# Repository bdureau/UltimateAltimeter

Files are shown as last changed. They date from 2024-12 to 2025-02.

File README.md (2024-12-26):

# UltimateAltimeter
This altimeter uses the TS-ESP32-S3 board without any additional components
You can find it on Aliexpress
https://vi.aliexpress.com/w/wholesale-TS%2525252dESP32%2525252dS3.html

That board has a BME280 sensor as well as a QMI8658 sensor.
You can measure the pressure (and derive the altitude from it). It also has a 3 axes accelerometer and well as gyroscope

The board is based on the Adafruit ESP32 S3 TFT Feather

https://cdn-learn.adafruit.com/downloads/pdf/adafruit-esp32-s3-tft-feather.pdf

https://github.com/adafruit/Adafruit-ESP32-S3-TFT-Feather-PCB/blob/main/Adafruit%20ESP32-S3%20TFT%20Feather%20Pinout.pdf

The board looks like this

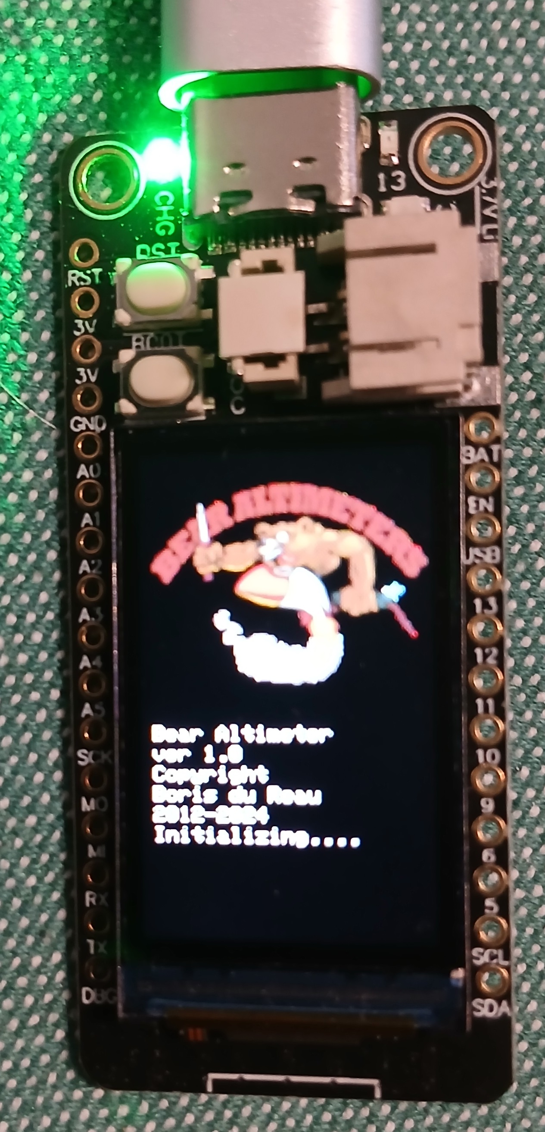
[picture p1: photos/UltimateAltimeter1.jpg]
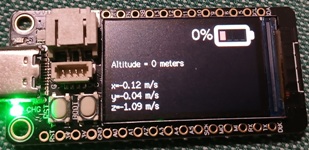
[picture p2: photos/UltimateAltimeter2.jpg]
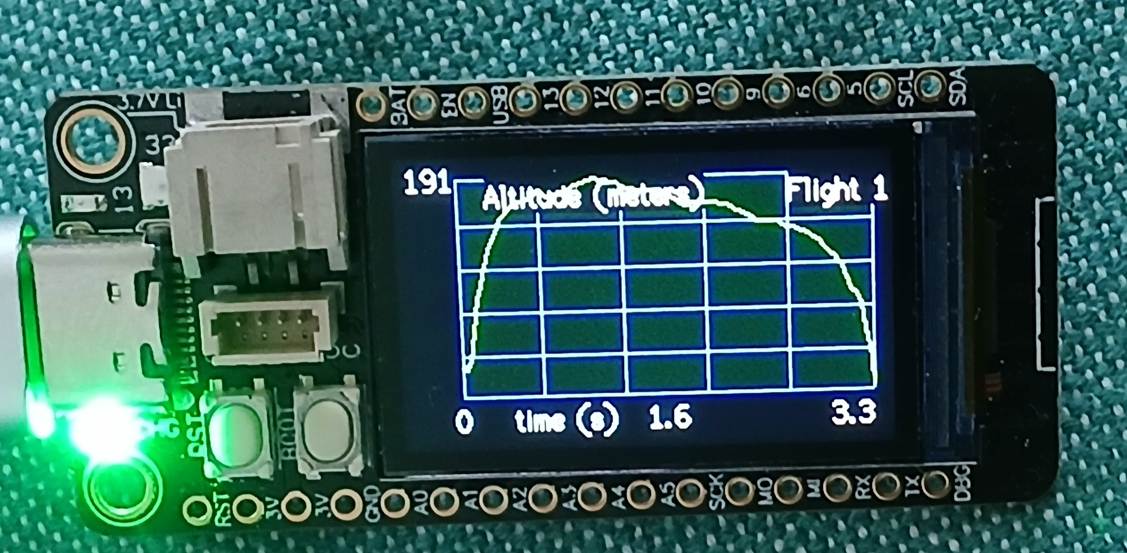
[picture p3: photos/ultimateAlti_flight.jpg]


# Building the code

You will need to download the Arduino ide from the [Arduino web site](https://www.arduino.cc/). 
Make sure that you install ESP32 support. 

2 versions are provided one that uses the preference library to store the flight.
https://github.com/bdureau/UltimateAltimeter/tree/main/UltimateAltimeter

and another one that uses the LittleFS library
https://github.com/bdureau/UltimateAltimeter/tree/main/UltimateAltimeterLittleFS

The project depend on the following libraries
  - TFT
  - Button2
  - TFT_eWidget
  - Preferences or LittleFS
  - BME280
  - SensorLib (used for the QMI8658 sensor)
    
You will need my fork of the TFT_eSPI
https://github.com/bdureau/TFT_eSPI

Compile with the following options:

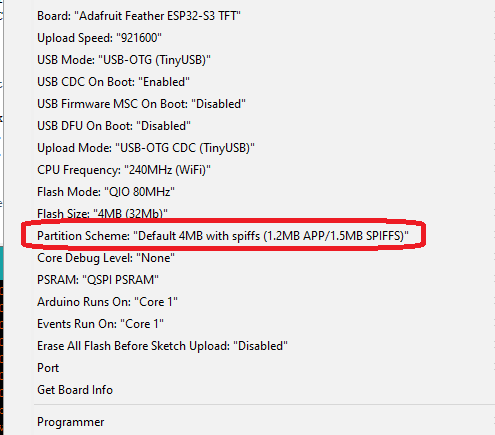
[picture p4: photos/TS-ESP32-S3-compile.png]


Prior to compiling go to the TFT_eSPI and open up the file User_Setup_Select.h

Comment out the following line
```
//#include <User_Setup.h> 
```
and uncomment the following line
```
#include <User_Setups/Setup400_Adafruit_Feather.h>
```

You will need to have the ESP32 board support version 2.0.14, anything higher than that may not work !!!

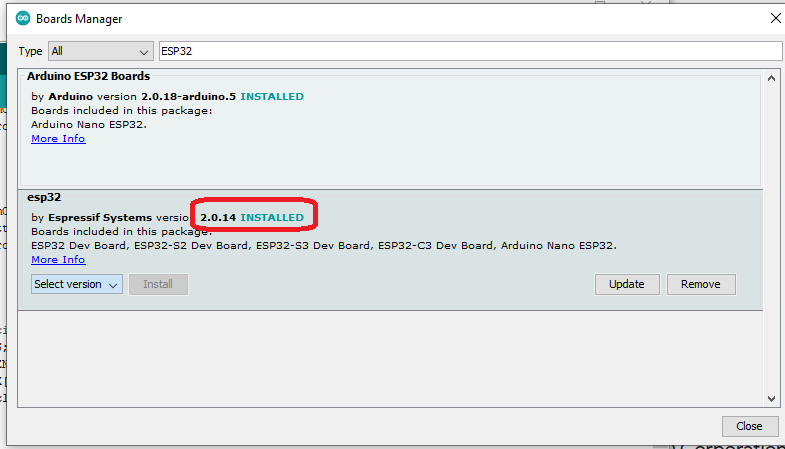
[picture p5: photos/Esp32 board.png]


# Contributing

If you want to contribute to the project just fork my project or send me some code. 

Report any issue or bug that you have

Suggestions and enhancement are welcome

The code is free for you to download and you do not need to buy anything from me. However it cost money to try out new boards, you need to buy them and fly them so if you want to financially help me you can donate via paypal

| Paypal | 
| ------ |
|  | 

# Disclaimer

I am not responsible for any damage that could happen. The code is provided as it is

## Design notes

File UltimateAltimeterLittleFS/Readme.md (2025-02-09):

This version uses the LittleFS library to store data. It might be slower but it can store a lot more data.
The following is recorded:
altitude, pressure, temperature, humidity and acceration on the 3 axis

Specific instruction to compile it
Make sure SPIFFS otherwise it will not store the data

As of version 0.5 I am switching to the BMP280 library from dvarrel (ver 1.0.3)
https://github.com/dvarrel/BMP280

use the following compilation directive #define USE_SLEEP_MODE to enable or disable the sleep mode

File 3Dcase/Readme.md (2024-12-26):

This is a case for the altimeter that can be 3D printed

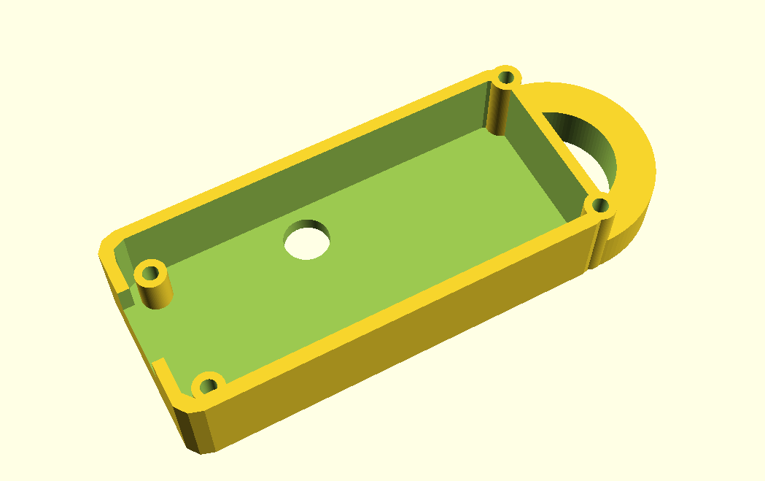
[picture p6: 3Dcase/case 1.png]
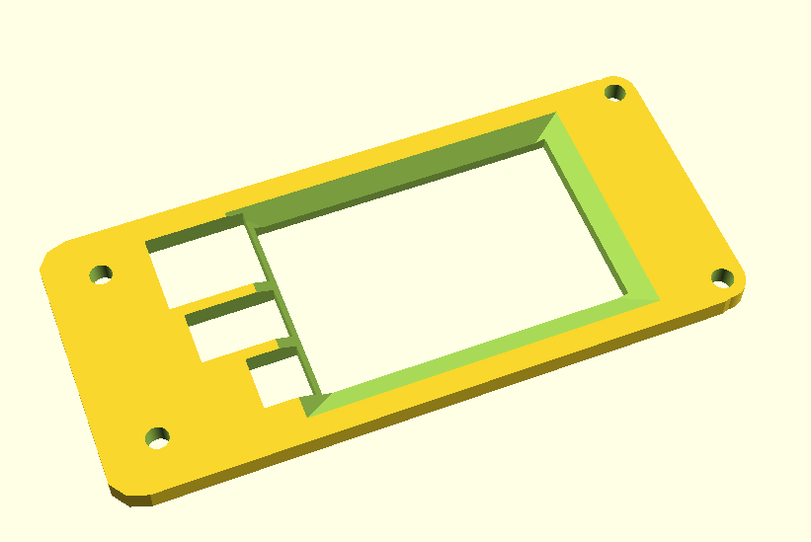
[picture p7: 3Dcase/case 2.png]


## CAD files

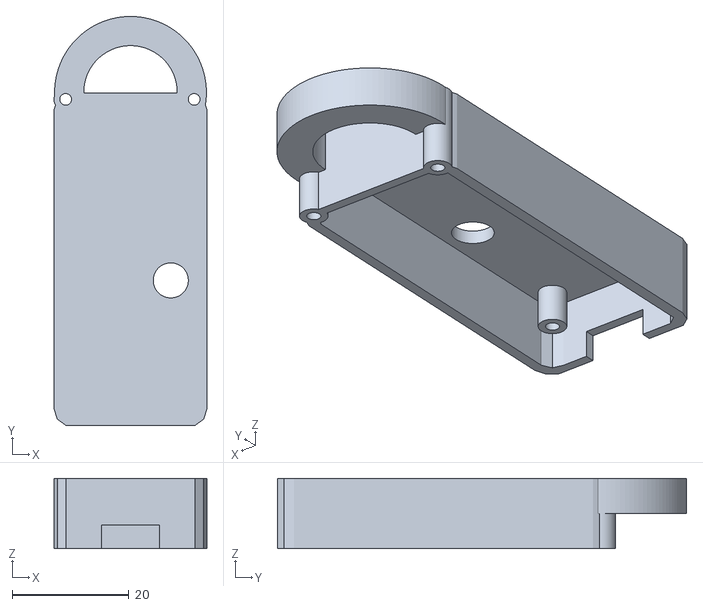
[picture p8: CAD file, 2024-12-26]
3Dcase/case_ts-esp32-s3altiV2.stl
26.2 x 70.1 x 12.0

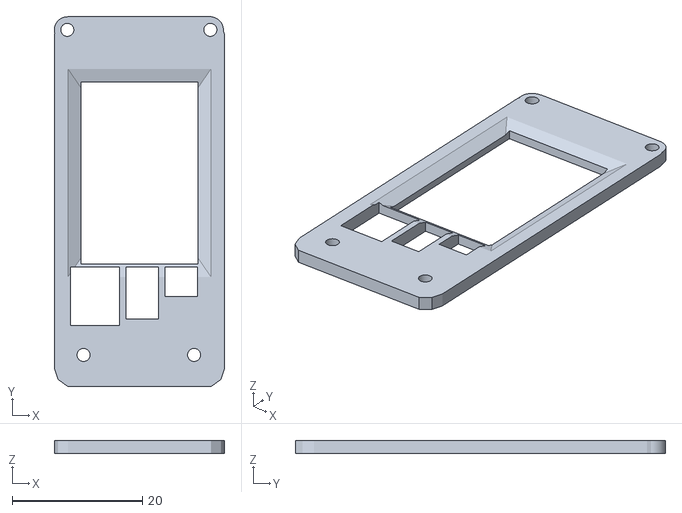
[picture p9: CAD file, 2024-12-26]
3Dcase/cover_case_ts-esp32-s3altiV2.stl
26.2 x 56.9 x 2.00

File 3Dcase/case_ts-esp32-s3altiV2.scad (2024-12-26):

/****************************************************************
* title: Alti case TS-ESP32-S3
* author: Boris du Reau
* version: 1.0
* date: 26/12/2024
* 
* Description: 
* Howto use it:
* Modify the variables values so that it fits to your rocket tube 
* then just click on "compile and render" 
* Note that all units ar metrics
*****************************************************************/

/* adjust variables here */ 

/* Do not modify anything after that unless you know what you are doing*/

module roundedcube(xdim, ydim, zdim,rdim) {
    hull(){
        translate([rdim, rdim,0]) cylinder(r=rdim, h=zdim);
        translate([xdim-rdim, rdim,0]) cylinder(r=rdim, h=zdim);
        translate([rdim, ydim -rdim,0]) cylinder(r=rdim, h=zdim);
        translate([xdim-rdim, ydim-rdim,0]) cylinder(r=rdim, h=zdim);
    }
}


module box() {
difference() {
    union() {
        difference() {
            union() {
                translate([0,0,-2])roundedcube(23 +(2*1.6), 54+ (2*1.6), 12,3); 
                difference() {
                    #translate ([(23 +(2*1.6))/2,54+ (2*1.6),4]) #cylinder(r=26/2, h=6, $fn=100);
                    #translate ([(23 +(2*1.6))/2,54+ (2*1.6),4]) #cylinder(r=16/2, h=6, $fn=100);
                }
            } 
            #translate ([1.6,1.6,-2]) roundedcube(23, 54, 10,2);  
        }     
        
        //case holes
        //#translate([0+2,2,4])cylinder(r=2, h=12, center = true, $fn =100);
        //#translate([0+28,2,4])cylinder(r=2, h=12, center = true, $fn =100);
        #translate([0+2,58-2,4])cylinder(r=2, h=12, center = true, $fn =100);
        #translate([0+24,58-2,4])cylinder(r=2, h=12, center = true, $fn =100); 
        
        //board holes
        #translate([0+2+2.5,2+3,6])cylinder(r=2, h=7, center = true, $fn =100);
        #translate([0+2+1.5+18,2+3,6])cylinder(r=2, h=7, center = true, $fn =100);
    }
    //case holes
    //#translate([0+2,2,0])cylinder(r=2/2, h=30, center = true, $fn =100);
    //#translate([0+28,2,0])cylinder(r=2/2, h=30, center = true, $fn =100);
    #translate([0+2,58-2,0])cylinder(r=2/2, h=30, center = true, $fn =100);
    #translate([0+24,58-2,0])cylinder(r=2/2, h=30, center = true, $fn =100);
    //board holes
    #translate([0+2+2.5, 2+3,5])cylinder(r=2/2, h=7, center = true, $fn =100);
    #translate([0+2+1.5+18, 2+3,5])cylinder(r=2/2, h=7, center = true, $fn =100);
    
    //usb port
    #translate([(23 +(2*1.6))/2,1,0])cube([10,2,4], center = true);
    //sensor hole
    #translate([20,25,4])cylinder(r=3, h=12, center = true, $fn =100);
}
    
}

module cover() {
difference() {
    union() {
        difference() {
            translate([0,0,0])roundedcube(23 +(2*1.6), 54+ (2*1.6), 2,3);     
        }
        //case holes
        //#translate([0+2,2,1])cylinder(r=2, h=2, center = true, $fn =100);
        //#translate([0+28,2,1])cylinder(r=2, h=2, center = true, $fn =100);
        #translate([0+2,55,1])cylinder(r=2, h=2, center = true, $fn =100);
        #translate([0+24,55,1])cylinder(r=2, h=2, center = true, $fn =100);
    }
    
    //case holes
    #translate([0+2,55,0])cylinder(r=2/2, h=30, center = true, $fn =100);
    #translate([0+24,55,0])cylinder(r=2/2, h=30, center = true, $fn =100);
    //board holes
    #translate([0+2+2.5,2+3,0])cylinder(r=2/2, h=30, center = true, $fn =100);
    #translate([0+2+1.5+18,2+3,0])cylinder(r=2/2, h=30, center = true, $fn =100);
    
    //window
    #translate([(23 +(2*1.6))/2,17.5+(31/2),2]) cube([18, 28, 4], center = true);
    #translate([(23 +(2*1.6))/2,17.5+(31/2),0])resize([22,32])rotate([0,0,45])cylinder(h=2, r1= 20, r2 = 32, $fn=4);
    
    #translate([2.5,9.5,0]) cube([7.5,9,4]);
    #translate([11,10.5,0]) cube([5,8,4]);
    #translate([17,14,0]) cube([5,4.5,4]);
} 
    
}

//box();
cover();

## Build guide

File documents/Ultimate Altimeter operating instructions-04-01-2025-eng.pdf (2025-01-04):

Ultimate Altimeter operating instructions

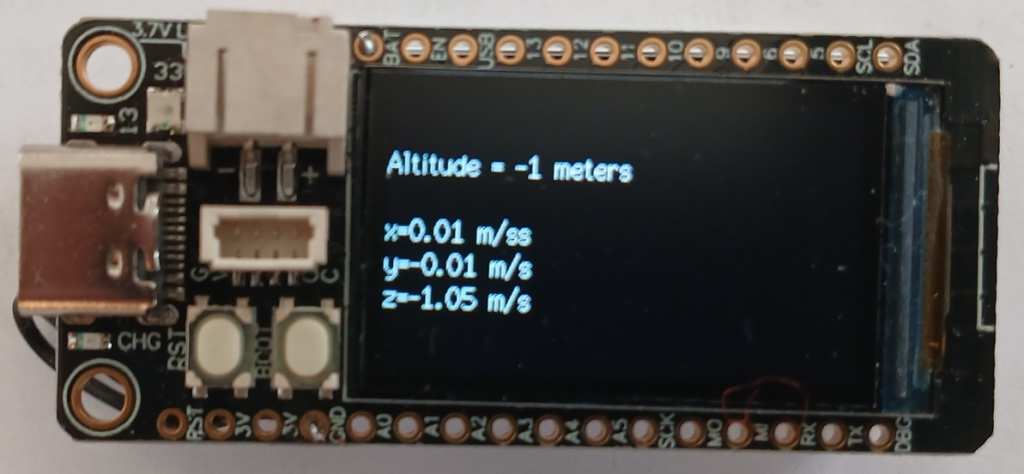
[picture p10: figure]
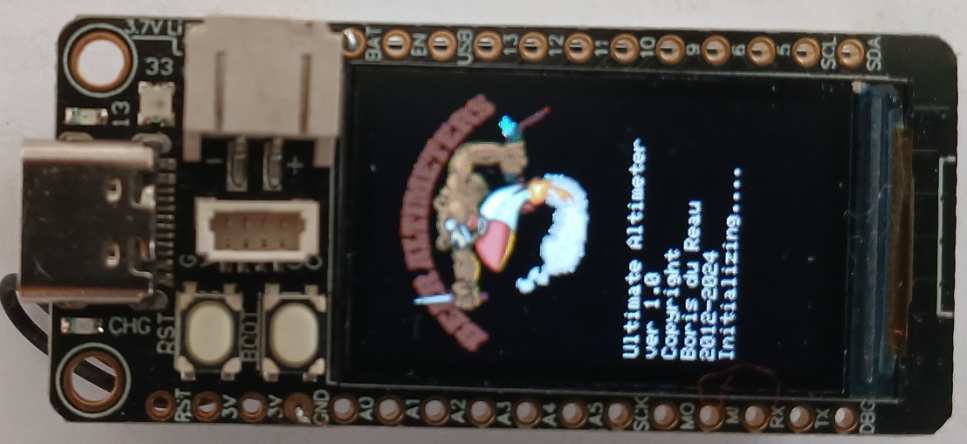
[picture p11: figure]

04/01/2025 | Copyright © Boris du Reau 2012-2025 | page 1

## Ultimate altimeter Operating instructions

Version | date | Author | Comments
1.0 | 04/01/2025 | Boris du Reau | Initial version

Rocket Type
Micro-max | Model Rocket | Mid power | High power | Water rocket
No | yes | yes | yes | yes

Category
Construction technic | Ground Support | Electronic | Other
| | X X

04/01/2025 | Copyright © Boris du Reau 2012-2025 | page 2

04/01/2025 | Copyright © Boris du Reau 2012-2025 | page 3

Goal

The goal of this document is to explain how to use the Ultimate altimeter that you just bought. The document assumes that you have already installed altimeters in a rocket payload bay.

Before your start
Remember that you can modify the program and behaviour of your altimeter.
The country where you live might not even allow the use of such device. You have to assume total legal responsibility for any damages or claims including personal injury that results from the use of this device. I shall not be responsible for the above. If you disagree with that, please do not build it or use it.

Related documentation
This document assumes that you have red the Bear Altimeters console documentation. This document will show you how to use the altimeter stand alone or with the console to view flights on a larger screen. I will also cover things such as flashing the altimeter from the Android Console.

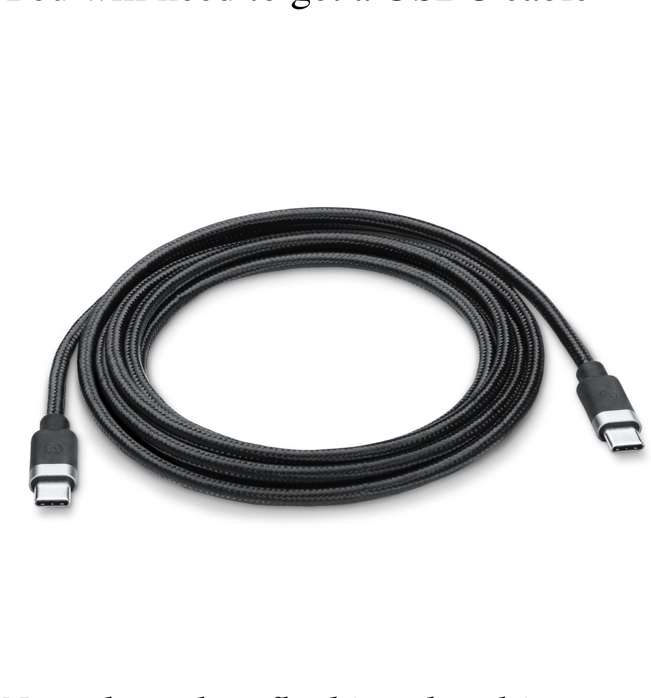
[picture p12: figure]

04/01/2025 | Copyright © Boris du Reau 2012-2025 | page 4

About the altimeter
The altimeter is made using a TS-ESP32-S3 board which contains an ESP32S3 micro controller from Espressif no additional custom board is required because the board already has a BME280 barometer and a QMI8658 sensor (accelerometer + gyroscope. The flights can be stored on the board no need of an additional EEPROM.
The firmware is written in C/C++ using the Arduino environment you can download the latest firmware from github
https://github.com/bdureau/UltimateAltimeter

If you are a developer you can build the firmware yourself using the Arduino environment and upload it to your board. Detailed instructions to build the code are available on the Github repository.

Flashing the altimeter firmware
The altimeter firmware can be flashed using the “BearConsole” application available on the Android playstore.
https://play.google.com/store/apps/details?id=com.altimeter.bdureau.bearconsole

Currently no application is available for Apple and I am not planning on doing any. Should any one want to write one the Android source code is available on my Github https://github.com/bdureau/BearConsole2

You will need to get a USBC cable

Note that when flashing the altimeter no need to configure the application to use USB, it will automatically do it because a USB cable is the only way to flash the altimeter, you cannot do it with a Bluetooth module.

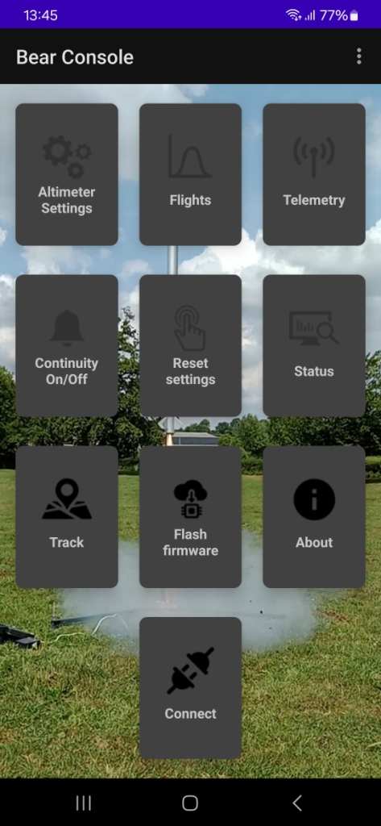
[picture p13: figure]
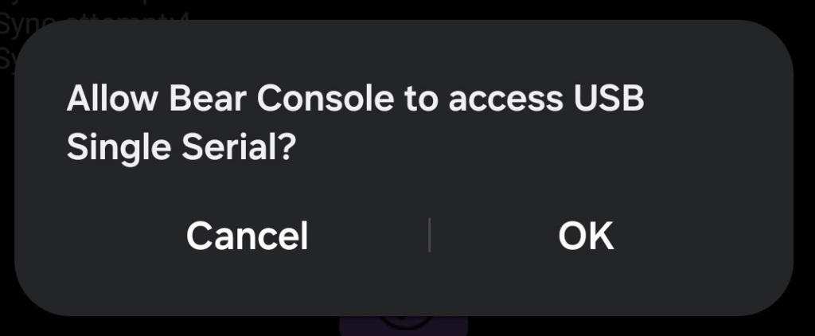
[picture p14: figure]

04/01/2025 | Copyright © Boris du Reau 2012-2025 | page 5

The following needs to be done to flash your board with a new firmware
- First install the application on an android device. Get it from the Android playstore https://play.google.com/store/apps/details?id=com.altimeter.bdureau.bearconsole
- Get a USB cable and connect your phone to the altimeter
- Open up the BearConsole application
- Tap on the flash firmware button
- Grant the permission

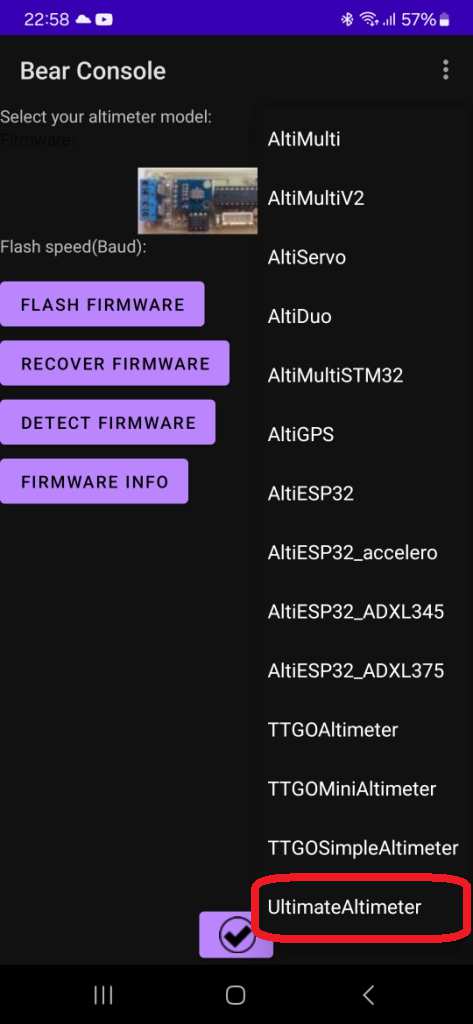
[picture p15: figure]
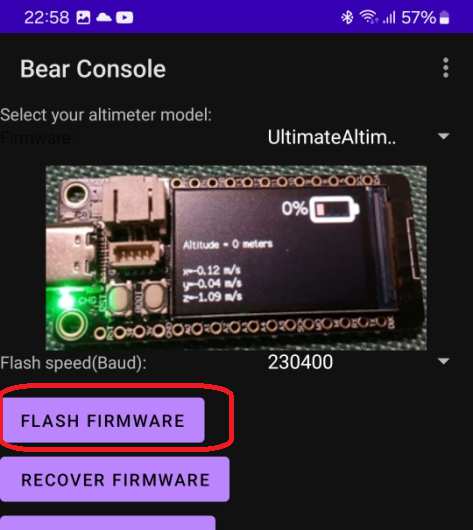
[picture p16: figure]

04/01/2025 | Copyright © Boris du Reau 2012-2025 | page 6
- Select your altimeter firmware. Make sure that you choose the appropriate firmware, if you don’t you will have unexpected behaviour.
- Tap on the flash firmware button

A popup will display with the firmware progress

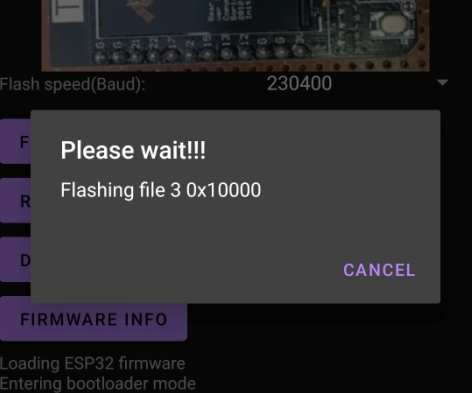
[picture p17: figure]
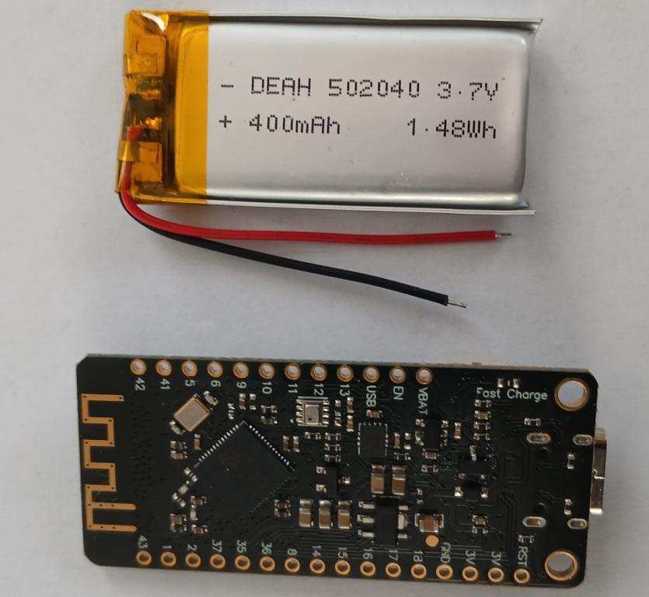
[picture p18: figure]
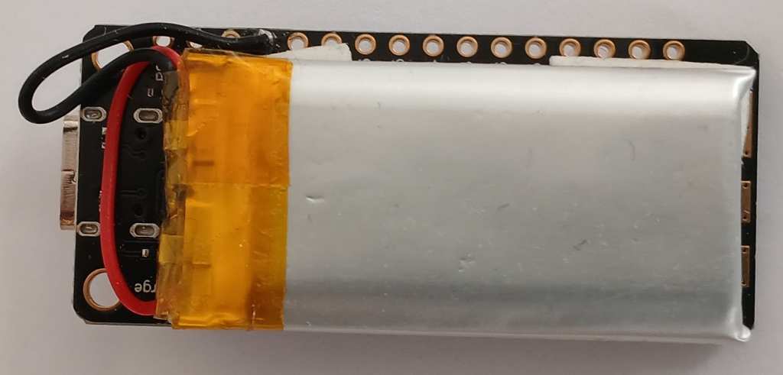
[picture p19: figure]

04/01/2025 | Copyright © Boris du Reau 2012-2025 | page 7

Flashing should take less than a minute when complete reset your altimeter.

Note that you need to make sure that the cable is connected during the entire upload of the firmware.

Choosing the power supply
The kit has been designed to use a 1S (3.7 Volts) battery. Using a poor quality battery may result in altimeter malfunction. You will need to get a JST plug compatible with your board or you can solder your 1S battery directly on the board (red wire on Vbat and black wire on GND). Be careful the TS-ESP32-S3 board JST plug is wired reverse; if you use a standard battery with a JST plug you will burn your board.

Charging the altimeter
The altimeter can be charged using a USBC cable and any USB port from a computer or from a USB charger. You will see the charge progress with the battery symbol.

Preparing the altimeter
When using the altimeter for the first time the altimeter must be initialized. First you need to blank the eeprom.
Power the altimeter by pressing button 2.
Then press button 2 for more than 10 seconds.
This will erase all flights.

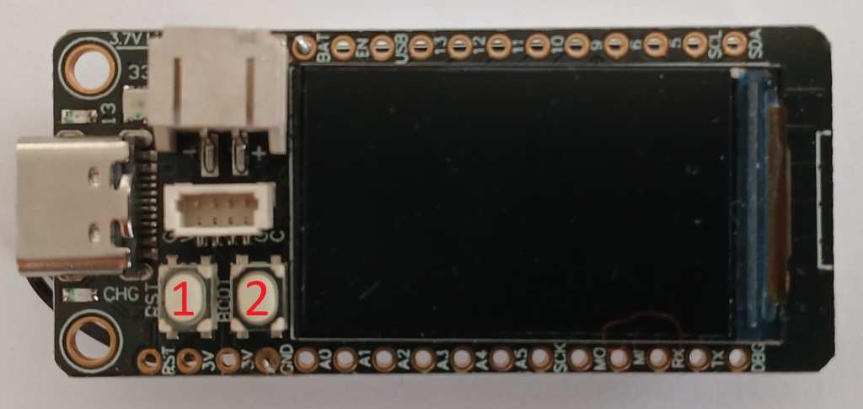
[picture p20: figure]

04/01/2025 | Copyright © Boris du Reau 2012-2025 | page 8

You are now left with an altimeter with no flights at all ready to be used.
Note that if you do not initialise your altimeter you may not be able to start recording flights.

Note that button 1 is the reset button; everything is done using only button 2.

Powering off the altimeter
You do not turn off your altimeter using a switch. By pressing button2 for more than 5 seconds you can put the altimeter in hibernate mode. Because it is in hibernate mode you need to make sure that you recharge your altimeter at least once a month otherwise your battery will get discharged under 3 volts and could be permanently damaged.
If you do not want to charge your altimeter, unplug your battery.

Installing the altimeter in the Rocket
The altimeter is very easy to install, just attach it to the nose cone. You will need to make sure that you have one or more vent holes to allow pressure exchanges.

Make sure that the electronic is protected from ejection smokes which are very corrosives and could damage the altimeter board very quickly.
However remember that you have a pressure sensor which needs to measure pressure changes to work out altitude changes… hence you need to drill a hole in your payload bay.

Using the altimeter
Now that you have everything installed in your rocket you can turn it on. The altimeter wait until lift off is detected. Lift off being by default reference altitude + 20 meters (this can be changed). Make sure that the altimeter is fully charged so that it can record the entire flight.

Reading your altimeter data without an Android device
You can read your data directly on the altimeter screen. The altimeter has been designed so that it can be used without an Android device; this will have limited functionalities but will allow you to quickly see your flight data when on the field.

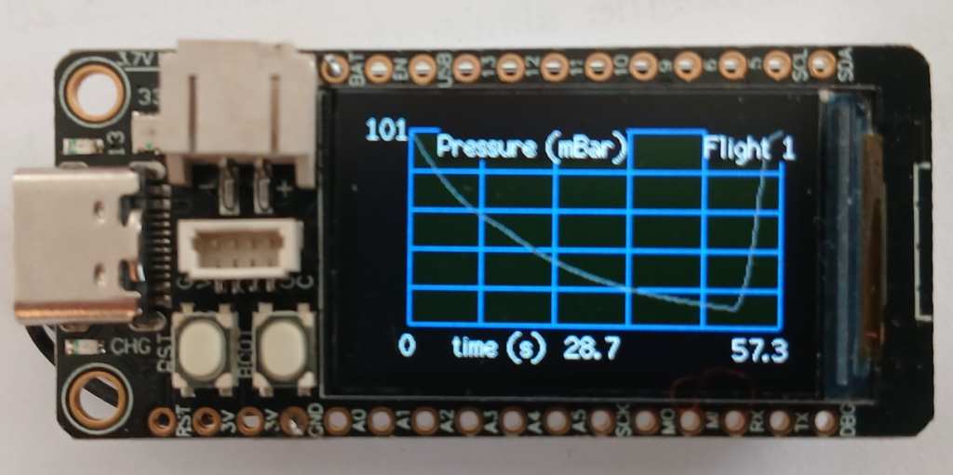
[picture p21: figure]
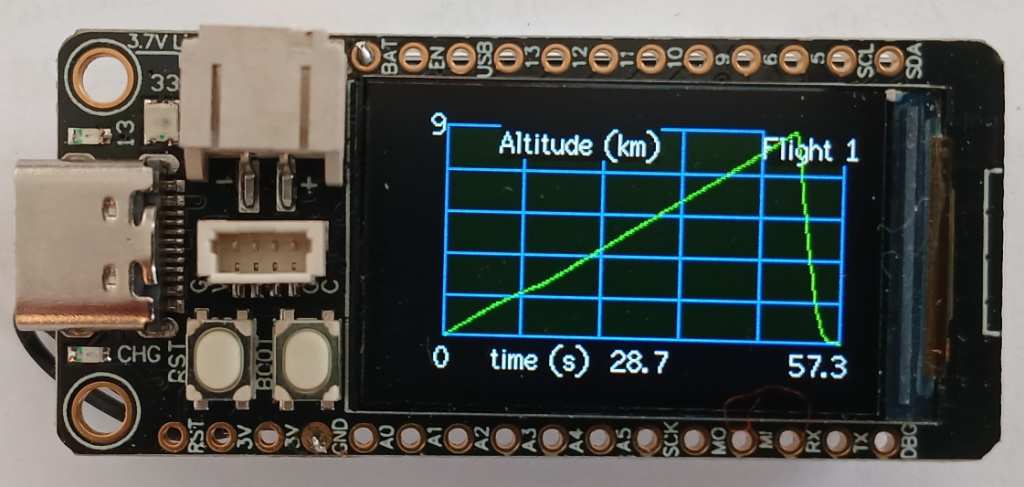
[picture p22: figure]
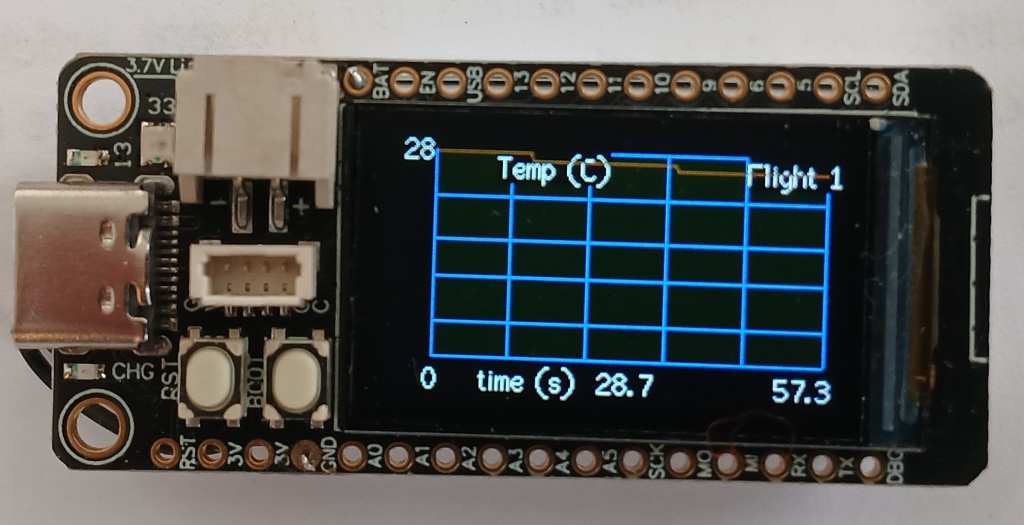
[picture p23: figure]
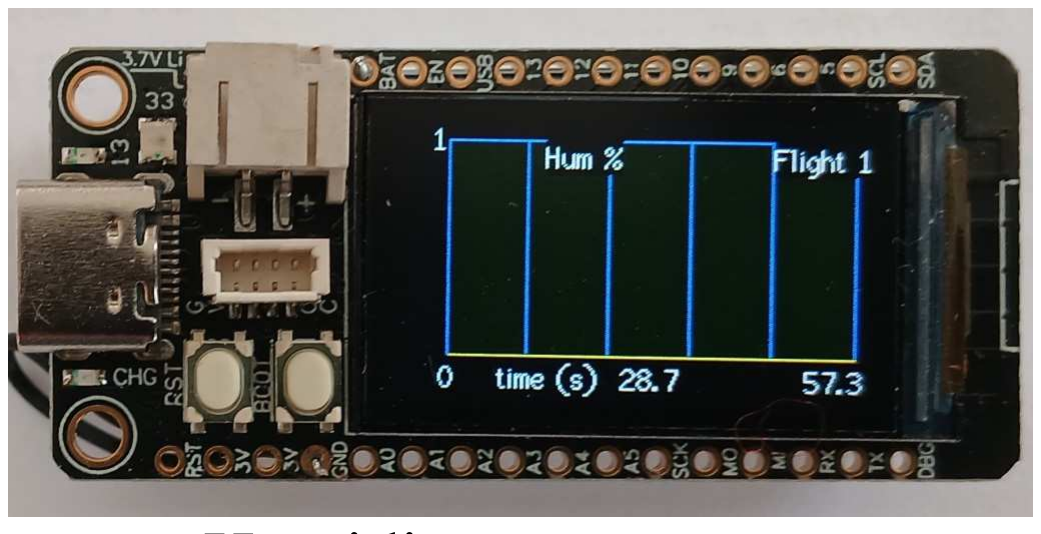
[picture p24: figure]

04/01/2025 | Copyright © Boris du Reau 2012-2025 | page 9

Retrieving your flight data
Press button 2 for more than 2 seconds will display the first flight. By default the altitude curve is shown.
To navigate between the flights curves short press button 2

The following data are available:

Altitude | Pressure

Acceleration on 3 axis

Humidity

Temperature

To exit the flight mode press button 2 for 2 seconds.

Erasing flight data
To prevent altimeter memory filling up you will have to erase your flights especially if those take a long time.
To clear all the flight press button 2 for more than 10 seconds

Reading your altimeter data with an Android device
If you have an Android device such as a tablet or a phone you can take the advantage of a bigger screen to see your flight data. This will also allow you to export them and share them with friends.
Application can be downloaded for the store
https://github.com/bdureau/BearConsole2

The altimeter uses a USB cable to communicate with any Android device.

Open the BearConsole application configuration to configure it to use USB rather than Bluetooth.

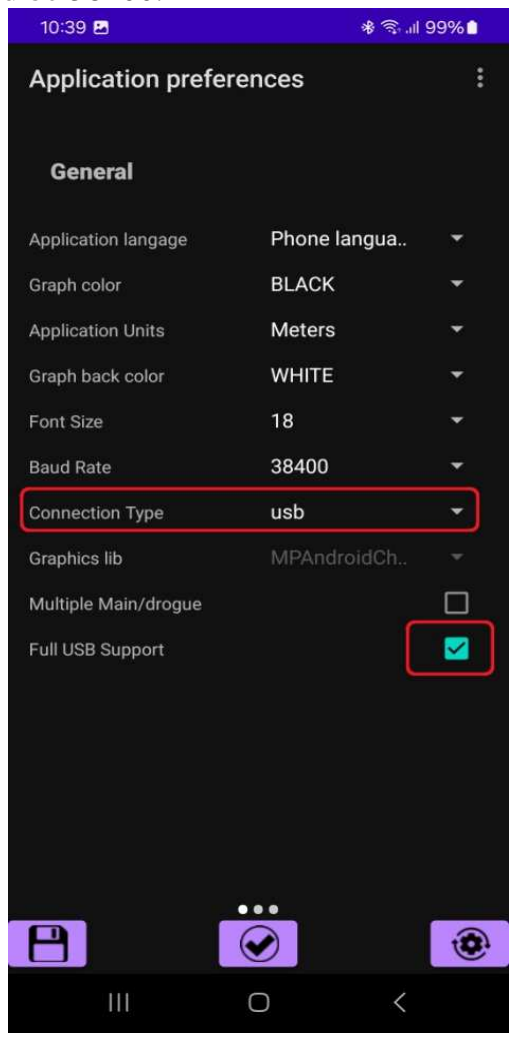
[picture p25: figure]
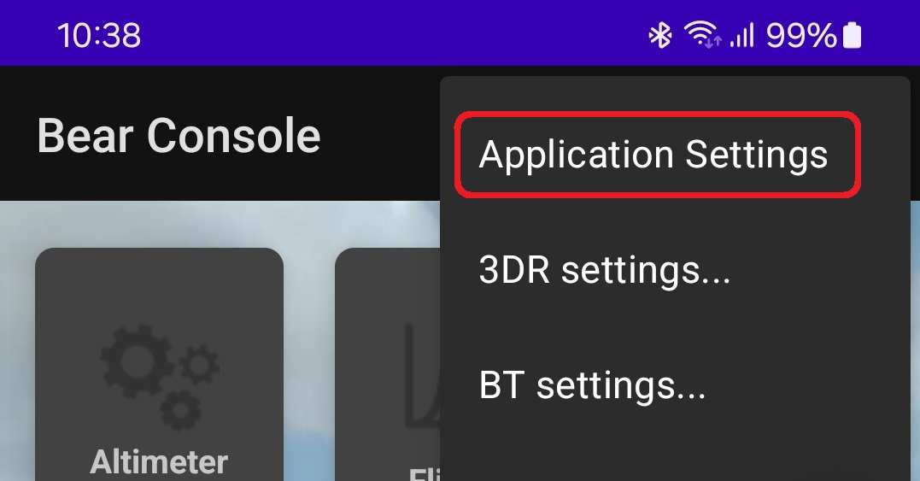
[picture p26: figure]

04/01/2025 | Copyright © Boris du Reau 2012-2025 | page 10

Using a USB cable
Connect your altimeter to your Android device using a USBC cable. Make sure that you configure your application so that it uses USB rather than Bluetooth and that option “Full usb support” is ticked. Lastly the baud rate should be 38400.

Then tap on save.

Connecting
On the main screen tap the connect button,

When connected the connect button will change its name to disconnect.

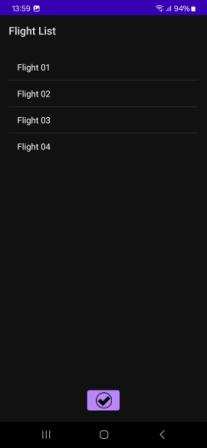
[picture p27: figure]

04/01/2025 | Copyright © Boris du Reau 2012-2025 | page 11

You can now using the applications functionalities that are available for the Ultimate altimeter.

Retrieving your flight data
Tap the flights button;

this will retrieve all your flights.

The select which flight you want to see.

When in the flight you can select which curve you want to see.

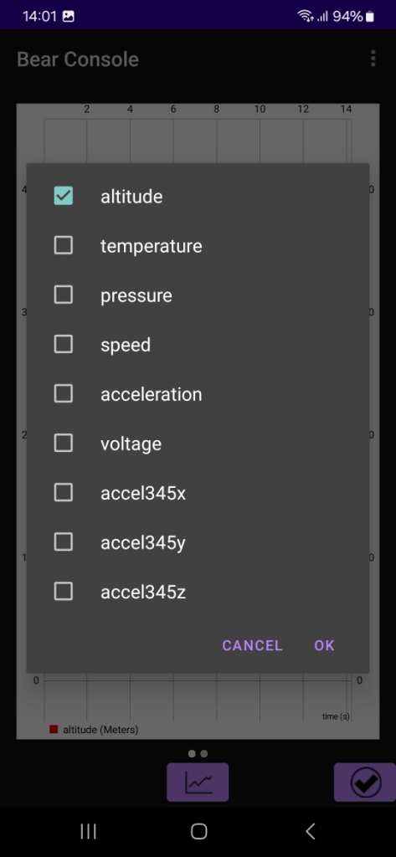
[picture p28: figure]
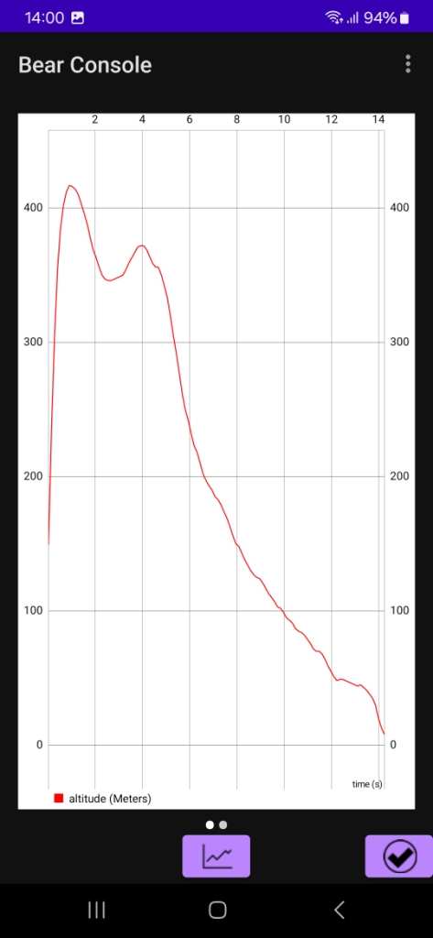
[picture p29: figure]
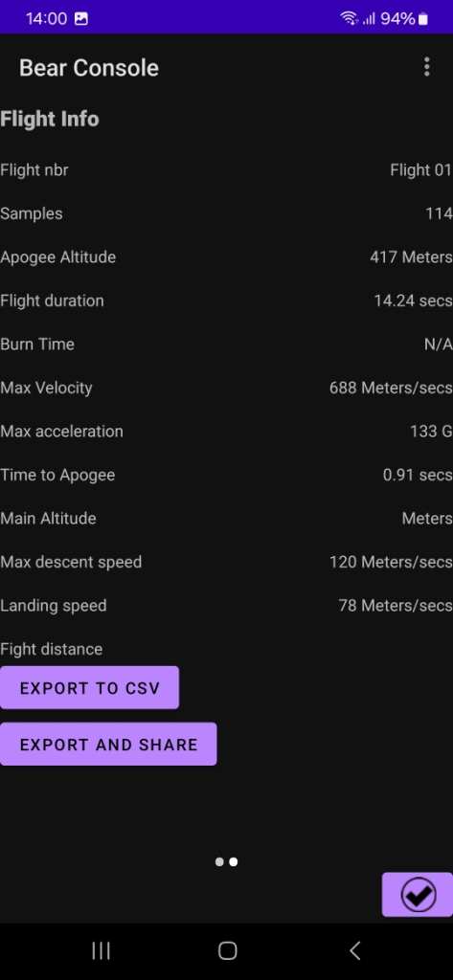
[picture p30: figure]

04/01/2025 | Copyright © Boris du Reau 2012-2025 | page 12

If you slide from right to left this will take you to the flight summary data

On any of the flight screen you can share the data using Whatsapp or email. You can share pictures of your flight as well as CSV data.

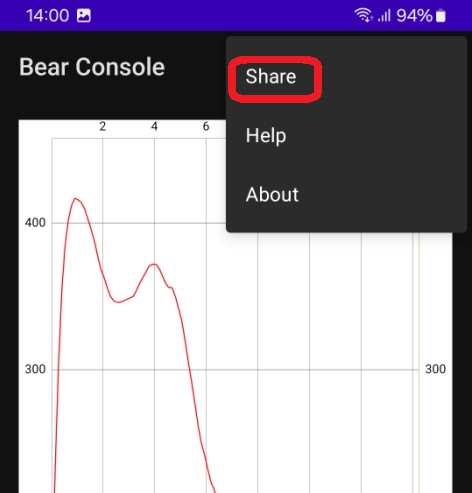
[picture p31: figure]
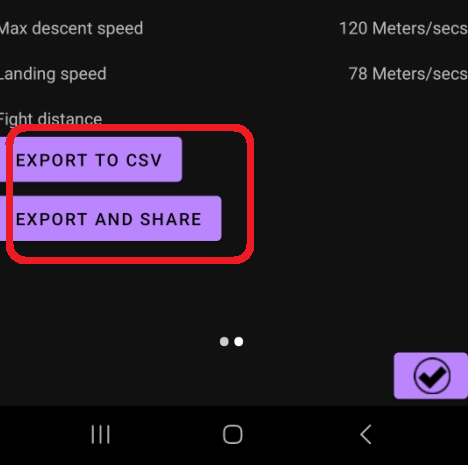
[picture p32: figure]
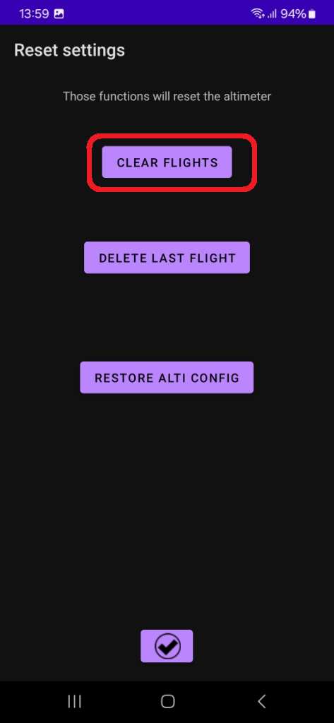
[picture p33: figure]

04/01/2025 | Copyright © Boris du Reau 2012-2025 | page 13

Erasing your flight data
To prevent your altimeter memory to be full which will stop you from recording new flights you need to erase your flight data. Space available on the board depends on the flight duration that you have recorded so far.
To erase flight data tap the “Reset settings” button

Then tap the “Clear Flights” button to erase all flights

04/01/2025 | Copyright © Boris du Reau 2012-2025 | page 14

Please refer to the on line help accessible from the console help menu. On some screens tool tips have been added to the screens to explain what it does. Currently the application is available in English French, Spanish, Italian, Portuguese, Russian, Dutch…. Should you want it in your own language I can provide a file with strings that can be translated and I will update the application with your own translations.

You can also refer to the Console documentation but it might not be up to date.

Altimeter box
A box to protect the altimeter that can be 3D printed has been designed with OpenScad and is available for download.
https://github.com/bdureau/UltimateAltimeter/tree/main/3Dcase

Testing the altimeter on the ground
In order to test all the firing sequences, I suggest that you build a very basic pressure chamber. It will cost you a couple of dollar and you will make sure that your altimeter is working before you fly your rocket.
Reading the data

Should you need additional help do not hesitate to ask, my contact details are on http://rocket.payload.free.fr/
or you can send me an email
boris.dureau@neuf.fr

Contributing to the board development
You do not have to be a developer to help on the project. Reporting bugs helps a lot to improve the altimeter. Interface suggestions will also improve the user experience when navigating. If you are good at making nice graphics this could also improve the look and feel of the application. If you have good writing skills you can help by contributing to the documentation.
Finally to allow people around the world to use the application in their own language you can help translating the application or documentation.

04/01/2025 | Copyright © Boris du Reau 2012-2025 | page 15

Trouble shooting

Because you have the ability to configure quite a lot of things on you altimeter things can go wrong and you might not be able to connect to your altimeter anymore…..

Do not worry; it is possible to reset the configuration of your altimeter.

Scenario 1: able to connect to the altimeter but the unable to modify the altimeter config without crashing the application

Solution:
Connect to the altimeter using the console (Bluetooth or cable) and reset the altimeter config to the default one.

Scenario 2: able to connect to the altimeter but the unable to load the flights without crashing the app.

Solution 1: You might be using Android version 8 or greater so you need to use a different graphic library. Go to the “Application Settings” menu and change the graphics lib to MPAndroidChart and click save.

Solution 2: You have probably stored flights with an older version of the firmware so you are unable to read them. You need to delete them all. In order to do that click on the “RESET SETTINGS” button and delete all flights.

Scenario 3: unable to connect to the altimeter

Solution 1: It could be because you have changed the altimeter baudrate and it is not matching the Bluetooth module baud rate anymore. You can try to connect using a cable and change the baudrate of the cable until you find the correct baud rate. Then you change the baud rate to 38400 and save the config. Alternatively you can reset the config.

Scenario 4: after upgrading the console the altimeter does not connect

Solution 1: you might need to flash the firmware from the console in order to make sure that your altimeter and firmware are in sync.

Scenario 5: unable to flash the altimeter

Solution: you might need to put the altimeter in boot mode before pressing the FLASH FIRMWARE button.

Scenario 6: Altimeter behaviour is not has expected

Solution 1: maybe the firmware is incorrect, reflash it was the correct one

04/01/2025 | Copyright © Boris du Reau 2012-2025 | page 16

Solution 2: rest the config to the default one

Scenario 7: cannot connect to the altimeter using Bluetooth

Solution 1: make sure that the connection type is Bluetooth

Solution 2: make sure that you have selected the correct Bluetooth module.

Scenario 8: cannot connect to the altimeter using the TTL cable

Solution 1: make sure that you have selected USB from the “Application settings” menu and that the seep is 38400 (unless you have changed it to something else).

If you experience any other issues that are not listed please contact me for advices. You will need to provide the following information:
- Altimeter model
- Firmware version
- Android version
- Console version

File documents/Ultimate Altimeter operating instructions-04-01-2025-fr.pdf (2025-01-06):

Ultimate Altimeter Manuel d'utilisation


06/01/2025 | Copyright © Boris du Reau 2012-2025 | page 1

## Ultimate altimeter Manuel d'utilisation

Version | date | Author | Comments
1.0 | 04/01/2025 | Boris du Reau | Initial version

Rocket Type
Micro-max | Model Rocket | Mid power | High power | Water rocket
No | yes | yes | yes | yes

Category
Construction technic | Ground Support | Electronic | Other
| | X X

06/01/2025 | Copyright © Boris du Reau 2012-2025 | page 2

06/01/2025 | Copyright © Boris du Reau 2012-2025 | page 3

Objectif

L'objectif de ce document est d'expliquer comment utiliser l'altimètre Ultimate que vous venez d'acquérir. Ce document suppose que vous avez déjà installé des altimètres dans la baie de charge utile d'une fusée.

Avant de commencer

Souvenez-vous que vous pouvez modifier le programme et le comportement de votre altimètre. Le pays où vous résidez peut ne pas autoriser l'utilisation d'un tel appareil. Vous assumez l'entière responsabilité légale de tout dommage ou réclamation, y compris les blessures corporelles, résultant de l'utilisation de cet appareil. Je ne saurais être tenu responsable des incidents mentionnés ci-dessus. Si vous n'acceptez pas cela, veuillez ne pas construire ou utiliser cet appareil.

Documentation associée

Ce document suppose que vous avez lu la documentation de la console Bear Altimeters. Ce document montre comment utiliser l'altimètre seul ou avec la console pour visualiser les vols sur un écran plus grand. Il couvre également des aspects tels que le flashage de l'altimètre depuis la console Android.

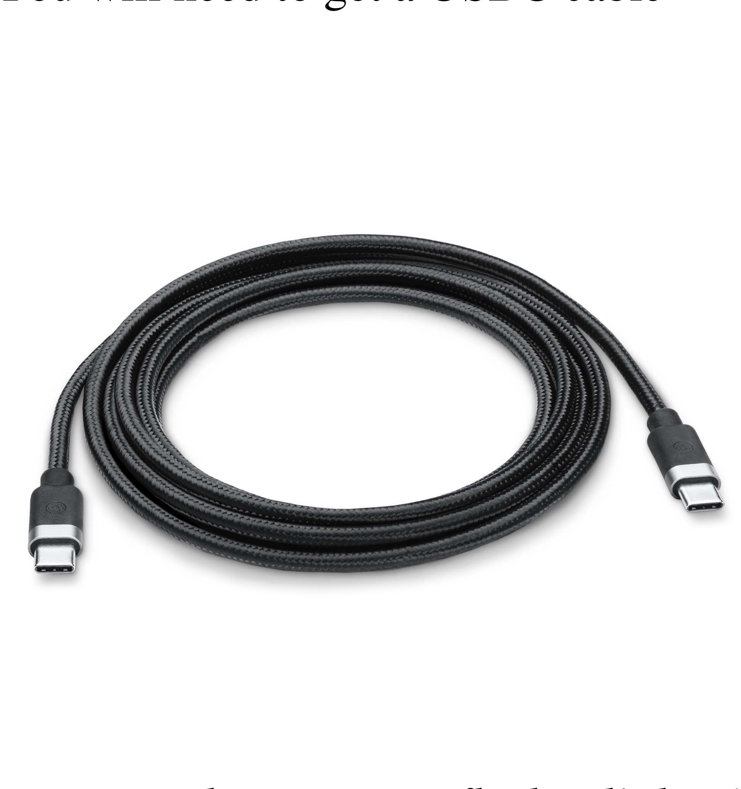
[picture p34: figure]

06/01/2025 | Copyright © Boris du Reau 2012-2025 | page 4

À propos de l'altimètre
L'altimètre est construit à l'aide d'une carte TS-ESP32-S3 qui intègre un microcontrôleur ESP32S3 d'Espressif.
Aucune carte supplémentaire n'est nécessaire car la carte est déjà équipée d'un baromètre BME280 et d'un capteur QMI8658 (accéléromètre + gyroscope). Les vols peuvent être stockés directement sur la carte, sans besoin de mémoire EEPROM supplémentaire.
Le firmware est écrit en C/C++ en utilisant l'environnement Arduino. Vous pouvez télécharger la dernière version du firmware sur GitHub : https://github.com/bdureau/UltimateAltimeter

Si vous êtes développeur, vous pouvez compiler vous-même le firmware en utilisant l'environnement Arduino et le télécharger sur votre carte. Les instructions détaillées pour construire le code sont disponibles sur le dépôt GitHub.

Flashage du firmware de l'altimètre
Le firmware de l'altimètre peut être flashé à l'aide de l'application BearConsole, disponible sur le Play Store Android : https://play.google.com/store/apps/details?id=com.altimeter.bdureau.bearconsole

Actuellement, aucune application n'est disponible pour Apple, et il n'est pas prévu d'en développer une. Cependant, toute personne intéressée peut utiliser le code source Android disponible sur mon GitHub :
https://github.com/bdureau/BearConsole2

You will need to get a USBC cable

Remarque lorsque vous flasher l’altimètre if n’est pas nécessaire de configurer l’application pour utiliser l’USB, cela sera fait automatiquement car le câble USB est le seul moyen de flasher l’altimètre, vous ne pouvez pas le faire en Bluetooth.


06/01/2025 | Copyright © Boris du Reau 2012-2025 | page 5

Étapes pour flasher votre carte avec un nouveau firmware

- Installer l'application sur un appareil Android depuis le Play Store.

https://play.google.com/store/apps/details?id=com.altimeter.bdureau.bearconsole

- Obtenir un câble USB-C et connecter votre téléphone à l'altimètre.
- Ouvrir l'application BearConsole
- Appuyer sur le bouton "Flash Firmware".
- Accorder les autorisations nécessaires


06/01/2025 | Copyright © Boris du Reau 2012-2025 | page 6
- Choisissez le firmware de votre altimetre. Assurez vous que vous choissez le bon firmware sinon cela ne fonctionnera pas.
- Appyez sur le boutton “flash firmware”


06/01/2025 | Copyright © Boris du Reau 2012-2025 | page 7

Une fenêtre contextuelle affichera la progression du flashage.

Le processus de flashage dure moins d'une minute. Une fois terminé, réinitialisez votre altimètre.

Assurez-vous que le câble reste connecté pendant tout le processus.

Choix de l'alimentation
Le kit est conçu pour fonctionner avec une batterie 1S (3,7 volts). Attention : Une batterie de mauvaise qualité peut entraîner un dysfonctionnement de l'altimètre. Vous devez utiliser un connecteur JST compatible avec votre carte ou souder directement la batterie 1S sur la carte (fil rouge sur Vbat et fil noir sur GND). Note importante : Le connecteur JST de la carte TS-ESP32-S3 est câblé à l'inverse. Si vous utilisez une batterie standard avec un connecteur JST, vous risquez de brûler votre carte

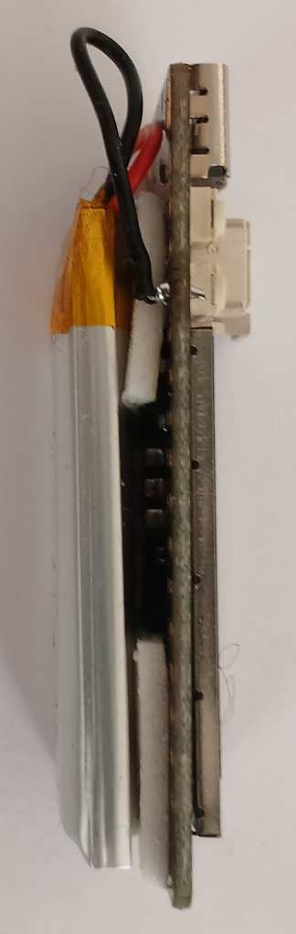
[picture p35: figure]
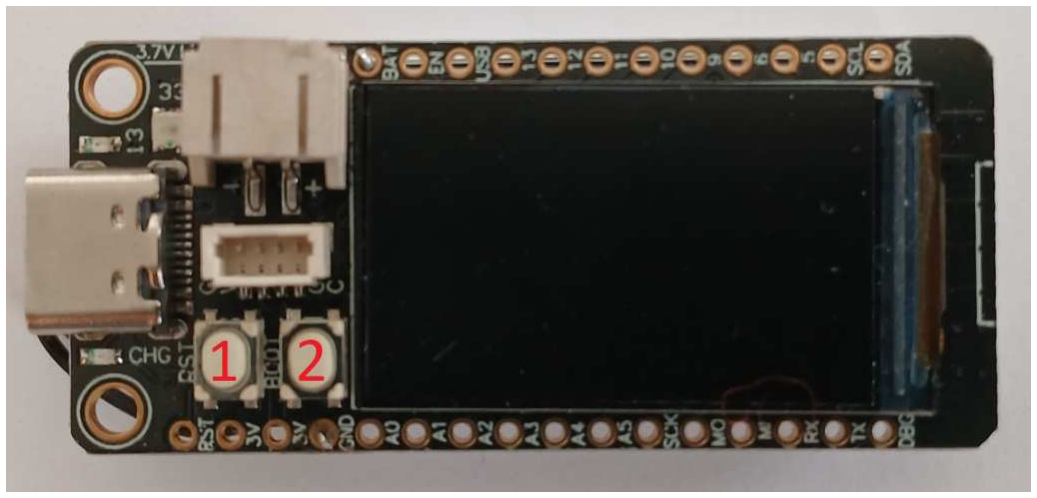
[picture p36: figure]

06/01/2025 | Copyright © Boris du Reau 2012-2025 | page 8

Chargement de l'altimètre

L'altimètre peut être chargé à l'aide d'un câble USB-C et de tout port USB d'ordinateur ou chargeur USB. L'écran de l'altimètre affichera une icône de batterie pour indiquer la progression du chargement.

Préparation de l'altimètre

Lors de la première utilisation, vous devez initialiser l'altimètre :

1. Allumez l'altimètre en appuyant sur le bouton 2.

### 2. Maintenez ensuite le bouton 2 enfoncé pendant plus de 10 secondes pour effacer

toutes les données de vol enregistrées.

Votre altimètre est maintenant prêt à être utilisé.

Remarque : Si vous n'initialisez pas votre altimètre, vous risquez de ne pas pouvoir enregistrer de nouveaux vols.

06/01/2025 | Copyright © Boris du Reau 2012-2025 | page 9

Mise hors tension de l'altimètre

L'altimètre ne possède pas d'interrupteur marche/arrêt.

- Maintenez le bouton 2 enfoncé pendant plus de 5 secondes pour mettre l'altimètre en mode hibernation.
- Rechargez l'altimètre au moins une fois par mois pour éviter d'endommager définitivement la batterie.

Si vous ne souhaitez pas recharger votre altimètre, débranchez la batterie.

Installation de l'altimètre dans la fusée

L'installation de l'altimètre est simple : attachez-le au cône de nez de la fusée.

Points importants :

- Assurez-vous de percer un ou plusieurs trous d'aération pour permettre les échanges de pression.
- Protégez l'électronique contre les fumées d'éjection, qui sont très corrosives et peuvent rapidement endommager la carte de l'altimètre.
- N'oubliez pas que le capteur de pression doit mesurer les changements de pression pour calculer l'altitude. Ainsi, un trou dans la baie de charge utile est indispensable.

Utilisation de l'altimètre

Une fois l'altimètre installé dans votre fusée :

1. Allumez-le.
L'altimètre attendra la détection du décollage. Par défaut, le décollage est défini comme une altitude de référence + 20 mètres (ce paramètre peut être modifié).

### 2. Assurez-vous que l'altimètre est entièrement chargé afin qu'il puisse enregistrer

tout le vol.

Lecture des données de l'altimètre sans appareil Android

Vous pouvez lire vos données directement sur l'écran de l'altimètre.
L'altimètre est conçu pour fonctionner sans appareil Android, offrant des fonctionnalités limitées mais permettant de consulter rapidement les données de vol sur le terrain.

Récupération des données de vol

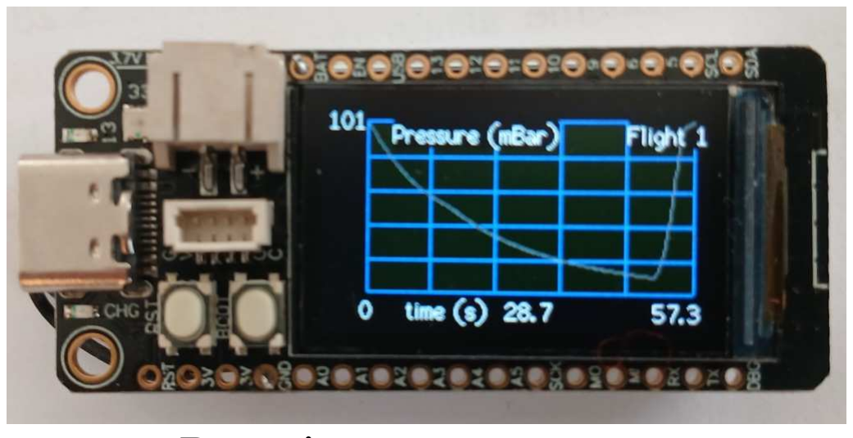
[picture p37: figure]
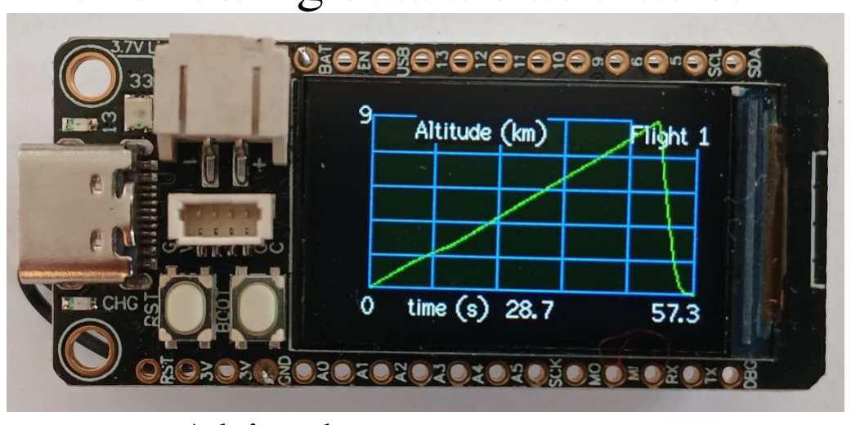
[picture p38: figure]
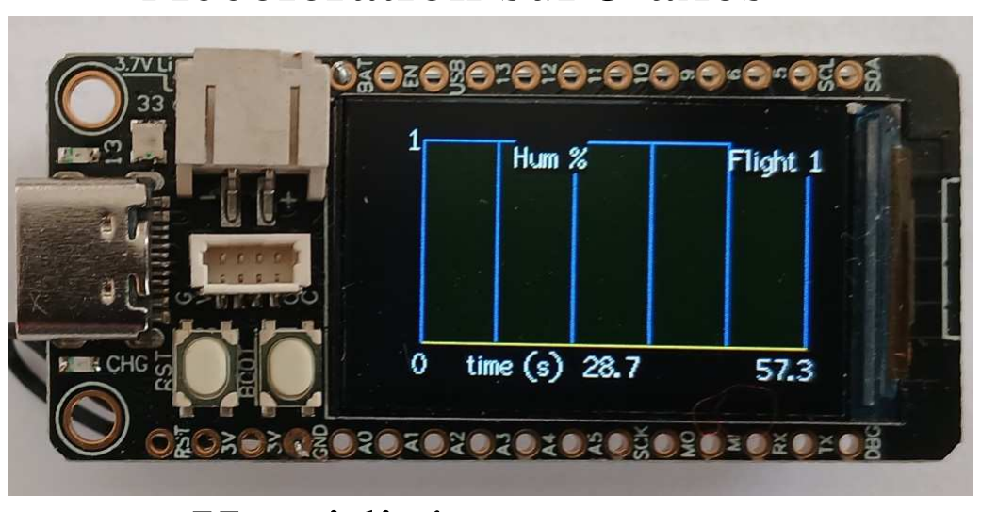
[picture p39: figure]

06/01/2025 | Copyright © Boris du Reau 2012-2025 | page 10

### 1. Appuyez sur le bouton 2 pendant plus de 2 secondes pour afficher le premier vol

enregistré. Par défaut, la courbe d'altitude est affichée.
2. Pour naviguer entre les courbes des vols, appuyez brièvement sur le bouton 2.

The following data are available:

Altitude | Pression

Accélération sur 3 axes

Humidité

Température

Pour quitter le mode vol, maintenez le bouton 2 enfoncé pendant 2 secondes.

Effacement des données de vol

Pour éviter de remplir la mémoire de l'altimètre, effacez régulièrement vos vols, surtout s'ils sont longs.

- Pour effacer tous les vols, maintenez le bouton 2 enfoncé pendant plus de 10 secondes.

Lecture des données de l'altimètre avec un appareil Android

Si vous possédez un appareil Android (téléphone ou tablette), vous pouvez bénéficier d'un écran plus grand pour consulter vos données de vol. Cela vous permet également de les exporter et de les partager avec vos amis.

### 1. Téléchargez l'application depuis le Play Store ou GitHub :

https://github.com/bdureau/BearConsole2

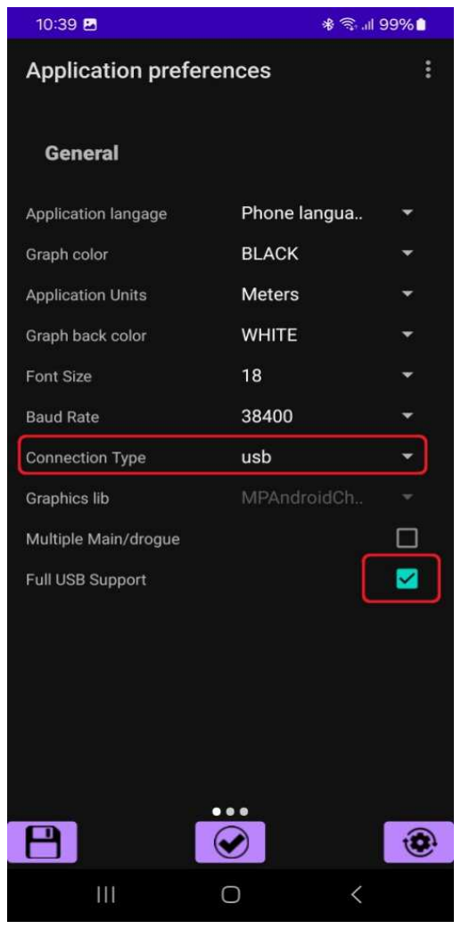
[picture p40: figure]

06/01/2025 | Copyright © Boris du Reau 2012-2025 | page 11
2. Connectez l'altimètre à votre appareil Android à l'aide d'un câble USB-C.
3. Configurez l'application pour utiliser l'USB plutôt que le Bluetooth.

Utilisation d'un câble USB

1. Connectez votre altimètre à l'appareil Android à l'aide d'un câble USB-C.

### 2. Configurez l'application pour utiliser l'USB :

- Cochez l'option "Full USB support".
- Réglez le débit en bauds sur 38400.

3 Appuyez sur "Save" pour enregistrer les paramètres.

06/01/2025 | Copyright © Boris du Reau 2012-2025 | page 12

Connexion et récupération des données
Sur l'écran principal, appuyez sur le bouton "Connecter".

Une fois connecté, le bouton changera en "Déconnecter".

You can now using the applications functionalities that are available for the Ultimate altimeter.

Récupération des données de vol

Appuyez sur le bouton "Vols" pour récupérer les vols.

Sélectionnez le vol souhaité,


06/01/2025 | Copyright © Boris du Reau 2012-2025 | page 13

puis choisissez la courbe à afficher.

Faites glisser l'écran de droite à gauche pour accéder aux données récapitulatives du vol.


06/01/2025 | Copyright © Boris du Reau 2012-2025 | page 14

Vous pouvez partager vos données de vol via WhatsApp ou e-mail, que ce soit sous forme d'images ou de fichiers CSV.

Effacement des données de vol sur Android

Pour éviter que la mémoire de l'altimètre ne soit pleine, ce qui empêcherait l'enregistrement de nouveaux vols, il est nécessaire d'effacer régulièrement les données de vol.

1. Dans l'application, appuyez sur le bouton "Reset Settings".
2. Ensuite, appuyez sur le bouton "Clear Flights" pour supprimer tous les vols.

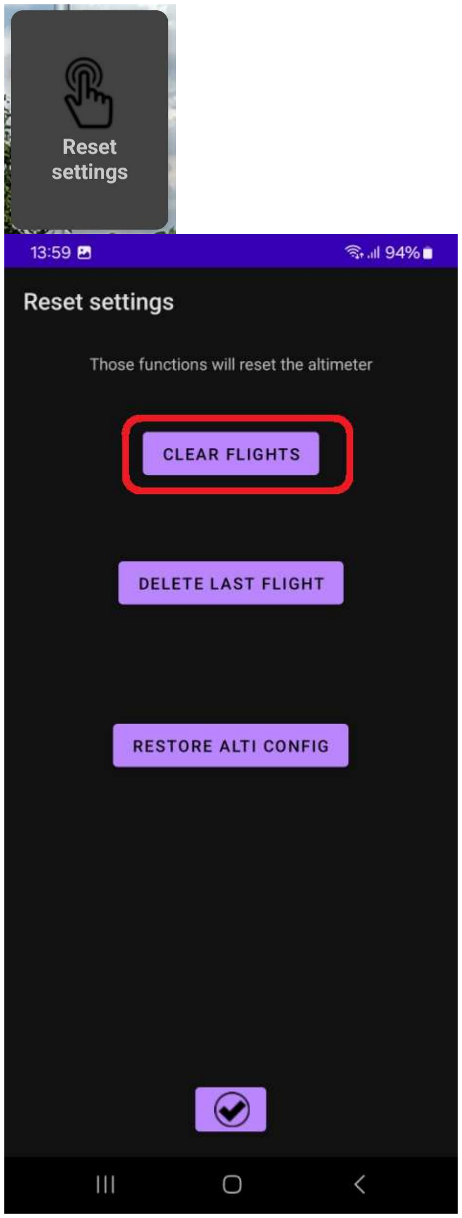
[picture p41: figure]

06/01/2025 | Copyright © Boris du Reau 2012-2025 | page 15

Veuillez consulter l'aide en ligne accessible depuis le menu d'aide de la console. Sur certains écrans, des info-bulles ont été ajoutées pour expliquer leurs fonctionnalités. Actuellement, l'application est disponible en anglais, français, espagnol, italien, portugais, russe, néerlandais… Si vous la souhaitez dans votre propre langue, je peux fournir un fichier contenant les chaînes à traduire, et je mettrai à jour l'application avec vos traductions.

Vous pouvez également consulter la documentation de la console, bien qu'elle puisse ne pas être à jour.

Boîtier de l'altimètre

Un boîtier de protection pour l'altimètre, conçu pour être imprimé en 3D, est disponible. Ce boîtier a été créé avec OpenScad et peut être téléchargé ici : https://github.com/bdureau/UltimateAltimeter/tree/main/3Dcase

06/01/2025 | Copyright © Boris du Reau 2012-2025 | page 16

Test de l'altimètre au sol

Pour tester toutes les séquences de déclenchement, il est recommandé de construire une chambre de pression basique.
Ce dispositif est peu coûteux et permet de s'assurer que l'altimètre fonctionne correctement avant de faire voler votre fusée.

Si vous avez besoin d’aide supplémentaire n’hesitez pas à me contacter. Les informations pour me contacter se trouvent sur
http://rocket.payload.free.fr/
ou vous pouvez m’envoyer un email
boris.dureau@neuf.fr

Contribuer au développement de la carte

Vous n'avez pas besoin d'être développeur pour contribuer au projet. Voici différentes manières d'aider :

- Signaler des bugs : cela aide à améliorer l'altimètre.
- Faire des suggestions d'interface : cela peut améliorer l'expérience utilisateur.
- Créer des graphismes : si vous êtes doué en design, cela pourrait améliorer l'esthétique de l'application.
- Contribuer à la documentation : si vous avez de bonnes compétences en rédaction.
- Traduire l'application ou la documentation : pour rendre l'application accessible dans d'autres langues.

06/01/2025 | Copyright © Boris du Reau 2012-2025 | page 17

Dépannage

Il est possible de rencontrer des problèmes en raison des nombreuses configurations possibles de l'altimètre. Voici des scénarios courants et leurs solutions :

Scénario 1 : Problèmes de configuration

Vous pouvez connecter l'altimètre mais ne pouvez pas modifier la configuration sans faire planter l'application.

Solution : Connectez l'altimètre via la console (Bluetooth ou câble) et réinitialisez la configuration aux paramètres par défaut.

Scénario 2 : Problèmes avec les données de vol

Vous pouvez connecter l'altimètre mais les vols ne se chargent pas ou font planter l'application.

Solution 1 : Si vous utilisez Android 8 ou une version ultérieure, changez la bibliothèque graphique dans le menu "Application Settings" en sélectionnant MPAndroidChart, puis sauvegardez.

Solution 2 : Si vous avez stocké des vols avec une ancienne version du firmware, supprimez toutes les données de vol en cliquant sur "Reset Settings" et en effaçant les vols.

Scénario 3 : Impossible de se connecter à l'altimètre

Cela peut être dû à un problème de vitesse de transmission des données (baud rate).

Solution : Connectez-vous avec un câble et ajustez le baud rate jusqu'à 38400, puis sauvegardez les paramètres.

Scénario 4 : Problème après une mise à jour de la console

Après une mise à jour, l'altimètre ne se connecte plus.

Solution : Flashez le firmware depuis la console pour synchroniser l'altimètre avec le logiciel.

Scénario 5 : Impossible de flasher l'altimètre

Solution : Mettez l'altimètre en mode boot avant d'appuyer sur le bouton "Flash Firmware".

Scénario 6 : Comportement inattendu de l'altimètre

Solution 1 : Reflashez le firmware avec la version correcte.
Solution 2 : Réinitialisez la configuration aux paramètres par défaut.

06/01/2025 | Copyright © Boris du Reau 2012-2025 | page 18

Scénario 7 : Problèmes avec la connexion Bluetooth

Solution 1 : Assurez-vous que le type de connexion est configuré sur Bluetooth.
Solution 2 : Vérifiez que le module Bluetooth correct est sélectionné.

Scénario 8 : Problèmes avec la connexion via un câble TTL
Solution : Sélectionnez USB dans le menu "Application Settings" et configurez la vitesse à 38400 (sauf si vous avez choisi une autre vitesse).

Besoin d'aide supplémentaire ?

Pour tout autre problème non listé, contactez-moi pour obtenir des conseils. Merci de fournir les informations suivantes :

- Modèle d'altimètre
- Version du firmware
- Version d'Android
- Version de la console

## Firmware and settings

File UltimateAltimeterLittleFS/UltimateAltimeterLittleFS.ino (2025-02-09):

/*
    UltimateAltimeter ver0.5
    Copyright Boris du Reau 2012-2025
    This is using a BME280 presure sensor
    for the accelerometer

    !!!IMPORTANT!!!!
    to compile it use the board "Adafruit Feather ESP32-S3 TFT"
    !!!IMPORTANT!!!!
    The flight is recorded on the board using LITTLE FS rather than the preferences library so that we can store longer flight

    Major changes on version 0.1
    Initial version of the code, this is re-using code from the TTGO board
    can display altitude, acceleration, temperature and pressure
    Major changes on version 0.2
    Code cleanup
    Added communication with the BearConsole application
    Major changes on version 0.3
    use the reset button to power on or of the board
    Major changes on version 0.4
    Added the status to the console app
    Removed humidity
    Fix to prevent stopping recording due to the ejection charge over pressure
    Major changes on version 0.5
    changes son that it uses the normal BMP280 library

*/
#include <SPI.h>
#include <TFT_eSPI.h>
#include <Button2.h>
#include <TFT_eWidget.h>
#include <driver/rtc_io.h>
#include <Wire.h>
#include <EnvironmentCalculations.h>
#include "SensorQMI8658.hpp"

#include <BMP280.h>
#include "kalman.h"
#include "logger.h"
#include "images/bear_altimeters128x128.h"
#define MAJOR_VERSION 0
#define MINOR_VERSION 5
#define BOARD_FIRMWARE "UltimateAltimeter"
#include <Preferences.h>
#include <WiFi.h>

//#define USE_SLEEP_MODE
//#define DEBUG
struct bmpValues {
  float pressure;
  float temperature;
  float altitude;
};
BMP280 bmp280;

#ifndef SENSOR_SDA
#define SENSOR_SDA  42
#endif

#ifndef SENSOR_SCL
#define SENSOR_SCL  41
#endif

logger flightLogger;

//////////////////////////////////////////////////////////////////////
// Global variables
//////////////////////////////////////////////////////////////////////

#define STATUS_HEIGHT_BAR 10

// Built in button GPIO - adjust for your board
#define BUTTON_GPIO GPIO_NUM_0

Button2 btn(BUTTON_GPIO); // Initialize the down button

TFT_eSPI tft = TFT_eSPI();
GraphWidget gr = GraphWidget(&tft);    // Graph widget
// Flight curves are drawn on tft using graph instance
TraceWidget trAltitude = TraceWidget(&gr);    // Altitude
TraceWidget trTemperature = TraceWidget(&gr);
TraceWidget trPressure = TraceWidget(&gr);
TraceWidget trAccelX = TraceWidget(&gr);    // Accel X
TraceWidget trAccelY = TraceWidget(&gr);    // Accel Y
TraceWidget trAccelZ = TraceWidget(&gr);    // Accel Z
TraceWidget trHumidity = TraceWidget(&gr);

// Assumed environmental values:
bool inGraph = false;

//ground level altitude
long initialAltitude;

//stop recording a maximum of 20 seconds after main has fired
long recordingTimeOut = 120 * 1000;
boolean canRecord = true;
boolean exitRecording = false;

long liftoffAltitude = 20;
long lastAltitude;
//current altitude
long currAltitude;
long diplayedFlightNbr = 0;
long currentCurveType = 0;
long apogeeAltitude;
//nbr of measures to do so that we are sure that apogee has been reached
unsigned long measures = 5;
boolean liftOff = false;
unsigned long initialTime = 0;
//telemetry
boolean telemetryEnable = false;
long lastTelemetry = 0;

SensorQMI8658 qmi;

IMUdata acc;
IMUdata gyr;

Kalman KalmanAltitude;

int onoroff = 2;

/*
   tft_output(int16_t x, int16_t y, uint16_t w, uint16_t h, uint16_t* bitmap)
*/
bool tft_output(int16_t x, int16_t y, uint16_t w, uint16_t h, uint16_t* bitmap)
{
  if ( y >= tft.height() ) return 0;
  tft.pushImage(x, y, w, h, bitmap);
  return 1;
}

/*
   button_init()

*/
void button_init()
{
  btn.setClickHandler([](Button2 & b) {
    // Down
    Serial.println(F("Button Down fast")); // It's called upCmd because it increases the index of an array. Visually that would mean the selector goes downwards.
    if (inGraph) {
      long lastFlightNbr = flightLogger.getLastFlightNbr();
      currentCurveType++;
      //Make sure we have not reach the last flight
      if ((lastFlightNbr > diplayedFlightNbr) & (currentCurveType > 4) ) {
        diplayedFlightNbr ++;
        currentCurveType = 0;
      } else {
        // if not lets go back to the first one if it exists
        if (!((lastFlightNbr < 1))) {
          if (currentCurveType > 4) {
            diplayedFlightNbr = 1;
            currentCurveType = 0;
          }
        }
      }
#ifdef DEBUG
      Serial.print("Flight:");
      Serial.println(diplayedFlightNbr);
      Serial.print("type:");
      Serial.println(currentCurveType);
#endif

      drawFlightNbr(diplayedFlightNbr, currentCurveType);
    }
  });

  btn.setLongClickHandler([](Button2 & b) {

    Serial.println("Button Down slow");
    unsigned int time = b.wasPressedFor();

    if (time >= 1000 & time < 3000) {
      if (!inGraph) {
        long lastFlightNbr = flightLogger.getLastFlightNbr();
#ifdef DEBUG
        Serial.print("lastFlightNbr:");
        Serial.println(lastFlightNbr);
#endif
        if (!(lastFlightNbr < 1)) {
          inGraph = true;
          diplayedFlightNbr = 1;
          drawFlightNbr(diplayedFlightNbr, currentCurveType);
        }
      } else {
        inGraph = false;
        tft.init();
        tft.fillScreen(TFT_BLACK);

        // Graph area is 200 pixels wide, 150 high, dark grey background
        gr.createGraph(200, 100, tft.color565(5, 5, 5));
        // x scale units is from 0 to 100, y scale units is 0 to 50
        gr.setGraphScale(0.0, 100.0, 0, 50.0);
      }
    }
    if (time >= 10000) {
      inGraph = false;
      tft.init();

      tft.fillScreen(TFT_BLACK);

      // Graph area is 200 pixels wide, 150 high, dark grey background
      gr.createGraph(200, 100, tft.color565(5, 5, 5));
      // x scale units is from 0 to 100, y scale units is 0 to 50
      gr.setGraphScale(0.0, 100.0, 0, 50.0);
      Serial.println("Erasing flights!!!");

      // erasing flights
      flightLogger.clearFlightList();
    }
  });
}

/*
   button_loop()

*/
void button_loop()
{
  // Check for button presses
  btn.loop();
}


void setup() {
  Wire.begin();
  Serial.begin(38400);
  Serial.println(F("Starting"));
  if (!flightLogger.initFileSystem()) {
    Serial.println(F("Failed to initialize file system"));
  } else {
    Serial.println(F("initFileSystem Ok"));
  }

  WiFi.mode(WIFI_OFF);
  flightLogger.initFlight();
  // turn on backlite
  pinMode(TFT_BACKLITE, OUTPUT);
  digitalWrite(TFT_BACKLITE, HIGH);

  // turn on the TFT / I2C power supply
  pinMode(TFT_I2C_POWER, OUTPUT);
  digitalWrite(TFT_I2C_POWER, HIGH);
  delay(10);

#ifdef USE_SLEEP_MODE
  Preferences preferences;
  preferences.begin("alti", false);
  onoroff = preferences.getUInt("onoroff", 0);
  if (onoroff == 0) {
    // system should turn on, but save onoroff = 1
    // Take no action
    preferences.putUInt("onoroff", 1);
    preferences.end();
  }
  else {
    // system should go to deep sleep, but save onoroff = 0
    // Turn off all power options and enter deep sleep forever.
    preferences.putUInt("onoroff", 0);
    preferences.end();
    // Disable accelerometer and gyro
    qmi.disableGyroscope();
    qmi.disableAccelerometer();

    pinMode(TFT_BACKLITE, OUTPUT);
    pinMode(TFT_I2C_POWER, OUTPUT);
    pinMode(4, OUTPUT);
    digitalWrite(TFT_BACKLITE, LOW);
    digitalWrite(TFT_I2C_POWER, LOW);
    pinMode(NEOPIXEL_POWER, OUTPUT);
    pinMode(41, OUTPUT);
    pinMode(42, OUTPUT);
    pinMode(26, OUTPUT);
    pinMode(7, OUTPUT);
    delay(100);
    digitalWrite(4, LOW);
    // Set pin states
    digitalWrite(TFT_BACKLITE, LOW);
    digitalWrite(TFT_I2C_POWER, LOW);
    digitalWrite(NEOPIXEL_POWER, LOW);
    // SDA SDL pins to the Stemma QT need to be set high as they have physical pull up resistors (2x10K)
    // PS Ram CS and TFT CS should be high.
    digitalWrite(41, HIGH);
    digitalWrite(42, HIGH);
    digitalWrite(26, HIGH);
    digitalWrite(7, HIGH);
    delay(10);
    gpio_deep_sleep_hold_en();
    gpio_hold_en((gpio_num_t) TFT_BACKLITE);
    gpio_hold_en((gpio_num_t) TFT_I2C_POWER);
    gpio_hold_en((gpio_num_t)NEOPIXEL_POWER);
    gpio_hold_en((gpio_num_t)41);
    gpio_hold_en((gpio_num_t)42);
    gpio_hold_en((gpio_num_t)26);
    gpio_hold_en((gpio_num_t)7);
    delay(2000);
    esp_deep_sleep_start();
  }
#endif

  tft.init();
  tft.fillScreen(TFT_BLACK);
  tft.setSwapBytes(true);

  tft.pushImage(6, 0, 128, 128, bear_altimeters128x128);
  tft.drawString("Ultimate Altimeter", 6, 135);
  tft.drawString("ver 1.0", 6, 145);
  tft.drawString("Copyright", 6, 155);
  tft.drawString("Boris du Reau", 6, 165);
  tft.drawString("2012-2025", 6, 175);
  tft.drawString("Initializing....", 6, 185);

  bmp280.begin();

  // let's do some dummy altitude reading
  // to initialise the Kalman filter
  for (int i = 0; i < 50; i++) {
    ReadAltitude();
  }

  //let's read the launch site altitude
  float sum = 0;
  for (int i = 0; i < 10; i++) {
    sum += ReadAltitude().altitude;
    delay(50);
  }
  initialAltitude = (long)(sum / 10.0);
  button_init();

  // Initialize QMI8658C sensor with provided configuration
  while (!qmi.begin(Wire, QMI8658_L_SLAVE_ADDRESS, SENSOR_SDA, SENSOR_SCL)) {
    tft.drawString("qmi error", 6, 195);
    delay(500);
  }
  delay(1000); // Delay for sensor initialization


  tft.setRotation(1);
  tft.fillScreen(TFT_BLACK);
  tft.drawString("altitude", 6, 0);
  // Graph area is 200 pixels wide, 150 high, dark grey background
  gr.createGraph(200, 100, tft.color565(5, 5, 5));
  // x scale units is from 0 to 100, y scale units is 0 to 50
  gr.setGraphScale(0.0, 100.0, 0, 50.0);

  tft.setTextColor(TFT_WHITE, TFT_BLACK);
  tft.fillScreen(TFT_BLACK);
  tft.setSwapBytes(true);
  tft.setTextFont(2);

  qmi.configAccelerometer(
    /*
       ACC_RANGE_2G
       ACC_RANGE_4G
       ACC_RANGE_8G
       ACC_RANGE_16G
    */
    SensorQMI8658::ACC_RANGE_4G,
    /*
       ACC_ODR_1000H
       ACC_ODR_500Hz
       ACC_ODR_250Hz
       ACC_ODR_125Hz
       ACC_ODR_62_5Hz
       ACC_ODR_31_25Hz
       ACC_ODR_LOWPOWER_128Hz
       ACC_ODR_LOWPOWER_21Hz
       ACC_ODR_LOWPOWER_11Hz
       ACC_ODR_LOWPOWER_3H
    */
    SensorQMI8658::ACC_ODR_1000Hz,
    /*
       LPF_MODE_0     //2.66% of ODR
       LPF_MODE_1     //3.63% of ODR
       LPF_MODE_2     //5.39% of ODR
       LPF_MODE_3     //13.37% of ODR
       LPF_OFF        // OFF Low-Pass Fitter
    */
    SensorQMI8658::LPF_MODE_0);

  qmi.configGyroscope(
    /*
      GYR_RANGE_16DPS
      GYR_RANGE_32DPS
      GYR_RANGE_64DPS
      GYR_RANGE_128DPS
      GYR_RANGE_256DPS
      GYR_RANGE_512DPS
      GYR_RANGE_1024DPS
    */
    SensorQMI8658::GYR_RANGE_64DPS,
    /*
       GYR_ODR_7174_4Hz
       GYR_ODR_3587_2Hz
       GYR_ODR_1793_6Hz
       GYR_ODR_896_8Hz
       GYR_ODR_448_4Hz
       GYR_ODR_224_2Hz
       GYR_ODR_112_1Hz
       GYR_ODR_56_05Hz
       GYR_ODR_28_025H
    */
    SensorQMI8658::GYR_ODR_896_8Hz,
    /*
       LPF_MODE_0     //2.66% of ODR
       LPF_MODE_1     //3.63% of ODR
       LPF_MODE_2     //5.39% of ODR
       LPF_MODE_3     //13.37% of ODR
       LPF_OFF        // OFF Low-Pass Fitter
    */
    SensorQMI8658::LPF_MODE_3);


  /*
    If both the accelerometer and gyroscope sensors are turned on at the same time,
    the output frequency will be based on the gyroscope output frequency.
    The example configuration is 896.8HZ output frequency,
    so the acceleration output frequency is also limited to 896.8HZ
  */
  qmi.enableGyroscope();
  qmi.enableAccelerometer();

}

/*
   loop()


*/
void loop() {

  char readVal = ' ';
  int i = 0;

  char commandbuffer[100];

  while ( readVal != ';')
  {
    button_loop();

    currAltitude = (long)ReadAltitude().altitude - initialAltitude;
    if (liftOff)
      SendTelemetry(millis() - initialTime, 200);
    if (!( currAltitude > liftoffAltitude) )
    {
      if (!inGraph) {
        SendTelemetry(0, 500);
        tft.setCursor (0, STATUS_HEIGHT_BAR);
        char Altitude [40];

        sprintf(Altitude, "Altitude = %i meters    ", currAltitude );
        tft.setCursor (0, STATUS_HEIGHT_BAR);
        tft.println("                                     ");
        tft.println(Altitude);

        char temp [15];
        if (qmi.getDataReady()) {
          if (qmi.getAccelerometer(acc.x, acc.y, acc.z)) {
            sprintf(temp, "x=%3.2f m/s", (float)acc.x );
            tft.println("");
            tft.println(temp);
            sprintf(temp, "y=%3.2f m/s", (float) acc.y );
            tft.println(temp);
            sprintf(temp, "z=%3.2f m/s", (float) acc.z );
            tft.println(temp);
          }
        }
      }

      while (Serial.available())
      {
        readVal = Serial.read();
        if (readVal != ';' )
        {
          if (readVal != '\n')
            commandbuffer[i++] = readVal;
        }
        else
        {
          commandbuffer[i++] = '\0';
          break;
        }
      }
    }
    else {
      //Serial.println("Recording!!!!");
      recordAltitude();
    }
  }
  interpretCommandBuffer(commandbuffer);
}



/*

   Read Altitude function for a BMP280 Bosch sensor


*/
bmpValues ReadAltitude() {
  bmpValues values;
  //Get pressure value
  uint32_t pressure = bmp280.getPressure();
  float temperature = bmp280.getTemperature();
  values.pressure = pressure;
  values.temperature = temperature;
  values.altitude = KalmanAltitude.KalmanCalc(bmp280.calAltitude(pressure, 1013.0));
  return values;
}


/*
   drawAxesXY(float minX, float maxX, float minY, float maxY )

*/
void drawAxesXY(float minX, float maxX, float minY, float maxY, int flightNbr, char *curveName ) {
  tft.fillScreen(TFT_BLACK);

  // x scale units is from 0 to 100, y scale units is 0 to 50
  gr.setGraphScale(minX, maxX, minY, maxY);
  // X grid starts at 0 with lines every 10 x-scale units
  // Y grid starts at 0 with lines every 10 y-scale units
  // blue grid
  gr.setGraphGrid(0.0, maxX / 5, 0.0, maxY / 5, TFT_BLUE);

  // Draw empty graph, top left corner at 20,10 on TFT
  gr.drawGraph(30, 10);

  // Draw the x axis scale
  tft.setTextDatum(TC_DATUM); // Top centre text datum
  tft.drawNumber(minX, gr.getPointX(minX), gr.getPointY(0) + 3);
  if (maxX < 1000) {
    tft.drawNumber(maxX / 2, gr.getPointX(maxX / 2), gr.getPointY(0) + 3);
    tft.drawNumber(maxX, gr.getPointX(maxX), gr.getPointY(0) + 3);
    tft.drawString("time(ms)", gr.getPointX(maxX / 4),  gr.getPointY(0) + 3);
  } else {
    char temp[10];
    sprintf(temp, "%3.1f",  maxX / 1000 / 2);
    tft.drawString(temp, gr.getPointX(maxX / 2),  gr.getPointY(0) + 3);
    sprintf(temp, "%3.1f",  maxX / 1000);
    tft.drawString(temp, gr.getPointX(maxX) - 10,  gr.getPointY(0) + 3);
    tft.drawString("time (s)", gr.getPointX(maxX / 4),  gr.getPointY(0) + 3);
  }
  char flight[15];
  sprintf(flight, "Flight %i  ",  flightNbr);
  tft.drawString(flight, gr.getPointX(maxX) - 10,  gr.getPointY(maxY));
  tft.drawString(curveName, gr.getPointX(maxX / 3), gr.getPointY(maxY));

  // Draw the y axis scale
  tft.setTextDatum(MR_DATUM); // Middle right text datum
  if (maxY < 1000)
    tft.drawNumber(maxY, gr.getPointX(0.0), gr.getPointY(maxY));
  else
    tft.drawNumber(round2dec(maxY / 1000), gr.getPointX(0.0), gr.getPointY(maxY));
}

long roundUp(float val) {
  long ret = (long)val;
  if (val > ret) {
    return ret + 1;
  }
  return ret;
}
float round2dec(float var)
{
  // 37.66666 * 100 =3766.66
  // 3766.66 + .5 =3767.16    for rounding off value
  // then type cast to int so value is 3767
  // then divided by 100 so the value converted into 37.67
  float value = (int)(var * 100 + .5);
  return (float)value / 100;
}
/*
   drawFlightNbr(int flightNbr, int curveType)

*/
void drawFlightNbr(int flightNbr, int curveType) {

  if (flightLogger.readFlight(flightNbr)) {
    FlightDataStruct* currentFlight;
    currentFlight = flightLogger.getFlightData();
    flightLogger.getFlightMinAndMax(flightNbr);

    //altitude
    if ( curveType == 0) {
      // Start altitude trace
      trAltitude.startTrace(TFT_GREEN);
      if ((float) flightLogger.getMaxAltitude() < 1000)
        drawAxesXY(0.0, flightLogger.getFlightDuration(), 0, (float) flightLogger.getMaxAltitude(), flightNbr, "Altitude (meters)" );
      else {
        drawAxesXY(0.0, flightLogger.getFlightDuration(), 0, (float) flightLogger.getMaxAltitude(), flightNbr, "Altitude (km)" );
      }
    }
    //accel
    if (curveType == 1) {
      trAccelX.startTrace(TFT_RED);
      trAccelY.startTrace(TFT_PURPLE);
      trAccelY.startTrace(TFT_YELLOW);
      float maxAccel = 0.0f;
      if (flightLogger.getMaxAccelX() > maxAccel)
        maxAccel = (float)flightLogger.getMaxAccelX();
      if (flightLogger.getMaxAccelY() > maxAccel)
        maxAccel = (float)flightLogger.getMaxAccelY();
      if (flightLogger.getMaxAccelZ() > maxAccel)
        maxAccel = (float)flightLogger.getMaxAccelZ();

      //Serial.println(maxAccel);
      drawAxesXY(0.0, flightLogger.getFlightDuration(), 0, (float) roundUp(maxAccel) , flightNbr, "Accel X,Y,Z (m/s)" );
    }
    //pressure
    if (curveType == 2) {
      trPressure.startTrace(TFT_GREY);
      //Serial.println(flightLogger.getMaxPressure());
      drawAxesXY(0.0, flightLogger.getFlightDuration(), 0, (float) roundUp(flightLogger.getMaxPressure()), flightNbr, "Pressure (mBar)" );
    }
    //temperature
    if (curveType == 3) {
      trTemperature.startTrace(TFT_BROWN);
      //Serial.println(flightLogger.getMaxTemperature());
      drawAxesXY(0.0, flightLogger.getFlightDuration(), 0, (float) roundUp(flightLogger.getMaxTemperature()), flightNbr, "Temp (°C)" );
    }
    //humidity
    /*if (curveType == 4) {
      trHumidity.startTrace(TFT_YELLOW);
      Serial.println(flightLogger.getMaxHumidity());
      drawAxesXY(0.0, flightLogger.getFlightDuration(), 0, (float) roundUp(flightLogger.getMaxHumidity() + 1), flightNbr, "Hum %" );
      }*/

    unsigned long currentTime = 0;

    for (long i = 0; i < flightLogger.getFlightSize(); i++)
    {
      currentTime = currentTime + currentFlight[i].diffTime; //logger.getFlightTimeData();

      //altitude
      if ( curveType == 0) {
        trAltitude.addPoint(currentTime, currentFlight[i].altitude);
      }

      if ( curveType == 1) {
        trAccelX.addPoint(currentTime, (float)currentFlight[i].accelX );
        trAccelY.addPoint(currentTime, (float)currentFlight[i].accelY );
        trAccelZ.addPoint(currentTime, (float)currentFlight[i].accelZ );
      }
      if ( curveType == 2) {
        trPressure.addPoint(currentTime, currentFlight[i].pressure);
      }
      if ( curveType == 3) {
        trTemperature.addPoint(currentTime, currentFlight[i].temperature);
      }
      /*if ( curveType == 4) {
        trHumidity.addPoint(currentTime, currentFlight[i].humidity);
        }*/
    }
  }
}

/*
   recordAltitude()

*/
void recordAltitude()
{
  long recordingTimeOut = 120 * 1000;
  unsigned long timeToApogee = 0;

  exitRecording = false;

  //long initialTime = 0;
  lastAltitude = 0;

  while (!exitRecording)
  {
    //read current altitude
    currAltitude = (ReadAltitude().altitude - initialAltitude);

    if ((currAltitude > liftoffAltitude) && !liftOff)
    {
      liftOff = true;
      SendTelemetry(0, 200);
      // save the time
      initialTime = millis();

      if (canRecord)
      {
        //init flight
        flightLogger.initFlight();
      }
    }
    unsigned long prevTime = 0;
    long prevAltitude = 0;
    // loop until we have reach an altitude of 3 meter
    while (liftOff)
    {
      unsigned long currentTime;
      unsigned long diffTime;

      currAltitude = (ReadAltitude().altitude - initialAltitude);

      currentTime = millis() - initialTime;

      prevAltitude = currAltitude;
      SendTelemetry(currentTime, 200);
      //display
      char Altitude [15];
      currAltitude = (long)ReadAltitude().altitude - initialAltitude;
      sprintf(Altitude, "Altitude = %i meters    ", currAltitude );
      tft.setCursor (0, STATUS_HEIGHT_BAR);

      tft.println("Recording in progress .....");
      tft.println(Altitude);

      // detect apogee
      if (currAltitude < lastAltitude) {
        measures = measures - 1;
        if (measures == 0)
        {
          apogeeAltitude = lastAltitude;
          timeToApogee = currentTime;
        }
      }
      else
      {
        lastAltitude = currAltitude;
        measures = 5;
      }

      char temp [15];

      if (qmi.getDataReady()) {
        if (qmi.getAccelerometer(acc.x, acc.y, acc.z)) {
          sprintf(temp, "x=%3.2f m/s", (float)acc.x );
          tft.println("");
          tft.println(temp);
          sprintf(temp, "y=%3.2f m/s", (float) acc.y );
          tft.println(temp);
          sprintf(temp, "z=%3.2f m/s", (float) acc.z );
          tft.println(temp);
        }
      }

      //record
      if (canRecord)
      {
        if ((currentTime - prevTime) > 150) {
          diffTime = currentTime - prevTime;
          prevTime = currentTime;

          flightLogger.setFlightTimeData(diffTime);
          flightLogger.setFlightAltitudeData(currAltitude);
          double temperature, pressure;
          //bmp.getTemperatureAndPressure(temperature, pressure);
          bmpValues val = ReadAltitude();
          flightLogger.setFlightTemperatureData((long) val.temperature);
          flightLogger.setFlightPressureData((long) val.pressure);

          if (qmi.getDataReady()) {
            if (qmi.getAccelerometer(acc.x, acc.y, acc.z)) {
              flightLogger.setAccelX(acc.x);
              flightLogger.setAccelY(acc.y);
              flightLogger.setAccelZ(acc.z);
            }
          }
          flightLogger.addToCurrentFlight();
        }
      }


      if ((canRecord && (timeToApogee > 0) && (currAltitude < 10) && (millis() - timeToApogee) > 2000) || (canRecord  && (millis() - initialTime) > recordingTimeOut) )
      {
        //end loging
        //save flight
        liftOff = false;
        flightLogger.writeFastFlight();

        exitRecording = true;
      }
    } // end while (liftoff)
  } //end while(recording)
}
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

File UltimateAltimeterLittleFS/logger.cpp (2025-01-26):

#include "logger.h"

logger::logger() {
  flightData = nullptr;
  dataPos = 0;
}

bool logger::initFileSystem() {
  if (!LittleFS.begin(false)) {
#ifdef DEBUG
    Serial.println("LITTLEFS Mount failed");
    Serial.println("Did not find filesystem; starting format");
#endif
    // format if begin fails
    if (!LittleFS.begin(true)) {
#ifdef DEBUG
      Serial.println("LITTLEFS mount failed");
      Serial.println("Formatting not possible");
#endif
      return false;
    } else {
      Serial.println("Formatting");
    }
  }
  return true;
}

bool logger::clearFlightList() {
#ifdef DEBUG
  Serial.println(F("Clearing all flights..."));
#endif
  // Open the root directory
  File root = LittleFS.open("/");
  if (!root || !root.isDirectory()) {
#ifdef DEBUG
    Serial.println(F("Failed to open the root directory"));
#endif
    return false;
  }

  // Iterate over all files in the root directory
  File file = root.openNextFile();
  while (file) {
#ifdef DEBUG
    Serial.print(F("Deleting file: "));
    Serial.println(file.name());
#endif
    // Delete the current file
    char fileName [15];
    sprintf(fileName, "/%s", file.name() );
    //make sure that you close the file so that it can be deleted
    file.close();
    if (LittleFS.remove(fileName)) {
#ifdef DEBUG
      Serial.println(F("Flight deleted successfully"));
#endif
    } else {
#ifdef DEBUG
      Serial.println(F("Failed to delete flight"));
#endif
    }

    // Move to the next file
    file = root.openNextFile();
  }
#ifdef DEBUG
  Serial.println(F("All files cleared."));
#endif
  return true;
}

bool logger::deleteLastFlight() {
  bool success = false;
  // Delete the current file
  char fileName [15];
  sprintf(fileName, "/flight%i", (int) getLastFlightNbr()  );

  if (LittleFS.remove(fileName)) {
#ifdef DEBUG
    Serial.println(F("Flight deleted successfully"));
#endif
    success = true;
  } else {
#ifdef DEBUG
    Serial.println(F("Failed to delete flight"));
#endif
    success = false;
  }
  return success;
}
long logger::getLastFlightNbr() {
  long maxFlightNumber = 0; // Default to 0 if no valid flight file is found

  // Open the root directory
  File root = LittleFS.open("/");
  if (!root || !root.isDirectory()) {
#ifdef DEBUG
    Serial.println(F("Failed to open the root directory"));
#endif
    return maxFlightNumber;
  }

  // Iterate over all files in the root directory
  File file = root.openNextFile();
  while (file) {
    String fileName = file.name();
#ifdef DEBUG
    Serial.print("Found file: ");
    Serial.println(fileName);
#endif

    // Check if the filename matches the pattern "flight<number>.json"
    if (fileName.startsWith("flight") && fileName.endsWith(".json")) {
      // Extract the flight number
      String numberPart = fileName.substring(6, fileName.length() - 5); // Extract between "flight" and ".json"
      int flightNumber = numberPart.toInt(); // Convert to integer

      // Update the maxFlightNumber if this one is larger
      if (flightNumber > maxFlightNumber) {
        maxFlightNumber = flightNumber;
      }
    }

    // Move to the next file
    file = root.openNextFile();
  }

  return maxFlightNumber;
}

bool logger::writeFastFlight() {
  return writeFlight(getLastFlightNbr() + 1);
}

bool logger::writeFlight(long flightNbr) {
  char flightName [15];
  sprintf(flightName, "/flight%i.json", flightNbr);

  DynamicJsonDocument doc(4096);
  JsonObject flight = doc.createNestedObject(flightName);

  for (long i = 0; i < dataPos; i++) {
    JsonObject record = flight.createNestedObject(String(i));
    record["diffTime"] = flightData[i].diffTime;
    record["altitude"] = flightData[i].altitude;
    record["accelX"] = flightData[i].accelX;
    record["accelY"] = flightData[i].accelY;
    record["accelZ"] = flightData[i].accelZ;
    record["pressure"] = flightData[i].pressure;
    //record["humidity"] = flightData[i].humidity;
    record["temperature"] = flightData[i].temperature;
  }

  //Serial.println(String(doc)));
  File file = LittleFS.open(flightName, "w");
  serializeJson(doc, file);
  file.close();

  return true;
}

bool logger::readFlight(long flightNbr) {
  char flightName [15];
  sprintf(flightName, "/flight%i.json", flightNbr);
#ifdef DEBUG
  Serial.println(flightName);
#endif
  File file = LittleFS.open(flightName, "r");
  if (!file) return false;

  DynamicJsonDocument doc(4096);
  deserializeJson(doc, file);
  file.close();

  JsonObject flight = doc[flightName];
  if (flight.isNull()) return false;

  dataPos = flight.size();
  if (flightData != nullptr) free(flightData);

  flightData = (FlightDataStruct*)malloc(sizeof(FlightDataStruct) * dataPos);
  if (!flightData) return false;

  long index = 0;
  for (JsonPair pair : flight) {
    JsonObject record = pair.value().as<JsonObject>();
    flightData[index].diffTime = record["diffTime"];
    flightData[index].altitude = record["altitude"];
    flightData[index].accelX = record["accelX"];
    flightData[index].accelY = record["accelY"];
    flightData[index].accelZ = record["accelZ"];
    flightData[index].pressure = record["pressure"];
    //flightData[index].humidity = record["humidity"];
    flightData[index].temperature = record["temperature"];
    index++;
  }

  return true;
}

bool logger::addToCurrentFlight() {
  FlightDataStruct* newFlightData = (FlightDataStruct*)realloc(flightData, (dataPos + 1) * sizeof(FlightDataStruct));
  if (!newFlightData) return false;

  flightData = newFlightData;
  flightData[dataPos] = currentRecord;
  dataPos++;
  return true;
}

bool logger::initFlight() {
  if (flightData != nullptr) free(flightData);
  flightData = nullptr;
  dataPos = 0;
  return true;
}

FlightDataStruct* logger::getFlightData() {
  return flightData;
}

void logger::setFlightTimeData(long diffTime) {
  currentRecord.diffTime = diffTime;
}

void logger::setFlightAltitudeData(long altitude) {
  currentRecord.altitude = altitude;
}
void logger::setFlightPressureData( long pressure) {
  currentRecord.pressure = pressure;
}

void logger::setFlightTemperatureData(long temperature) {
  currentRecord.temperature = temperature;
}

/*void logger::setFlightHumidityData( long humidity) {
  currentRecord.humidity = humidity;
}*/

void logger::setAccelX(float accelX) {
  currentRecord.accelX = accelX;
}

void logger::setAccelY(float accelY) {
  currentRecord.accelY = accelY;
}

void logger::setAccelZ(float accelZ) {
  currentRecord.accelZ = accelZ;
}

long logger::getFlightSize() {
  return dataPos;
}
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
